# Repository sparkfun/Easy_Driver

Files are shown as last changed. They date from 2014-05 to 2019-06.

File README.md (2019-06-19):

Easy Driver
===========

Easy Driver

[*Easy Driver (ROB-12779)*](https://www.sparkfun.com/products/12779)

The EasyDriver is a simple to use stepper motor driver, compatible with anything that can output a digital 0 to 5V pulse (or 0 to 3.3V pulse if you solder SJ2 closed on the EasyDriver). 
The EasyDriver requires a 7V to 20V supply to power the motor and can power any voltage of stepper motor.

Repository Contents
-------------------
* **/Firmware** - Any firmware that the part ships with, 
* **/Hardware** - All Eagle design files (.brd, .sch, .STL)
* **/Production** - Test bed files and production panel files

Documentation
--------------

* **[Hookup Guide](https://learn.sparkfun.com/tutorials/easy-driver-hook-up-guide)** - Basic hookup guide for the Easy Driver.
* **[Brian Schmalz: Easy Driver](http://schmalzhaus.com/EasyDriver/)** - More specs and FAQ.

License Information
-------------------

_Note: This product is a collaboration with Brian Schmalz. A portion of each sales goes back to him for product support and continued development._

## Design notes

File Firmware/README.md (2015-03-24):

SparkFun Easy Driver Example Code
======================================

Repository Contents
-------------------
* **/Arduija_Demo** - Firmware for the [Arduija Project](https://www.sparkfun.com/news/1631). 
* **/SparkFun_Easy_Driver_Basic_Demo** - Firmware for the [Easy Driver Hookup Guide](https://learn.sparkfun.com/tutorials/easy-driver-hook-up-guide).
* **/EasyDriver_Example1** -Example 1 from SchmalzHaus. 
* **/EasyDriver_Example2** -Example 2 from SchmalzHaus. 
* **/EasyDriver_Example3** -Example 3 from SchmalzHaus. 
* **/EasyDriver_Example4** -Example 4 from SchmalzHaus. 
* **/EasyDriver_Example5** -Example 5 from SchmalzHaus.

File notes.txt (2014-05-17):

EasyDriver Notes.txt

A file to keep thoughts about each version, test results, changes, etc.

10/27/2013 (Just ideas/wishes at this point)
	For v4.5, add current limiting resistors to all inputs
	For v4.5, add pull downs to STEP and DIR (ALL inputs have pull down or pull ups)
	For v4.5, add P-FET reverse polarity protection
	For v4.5, make 3.3/5 switch a cuttable jumper + .1" header for easy re-setting (change SJ1 and SJ2)
	
02/25/2014
	SparkFun requested:
	For v4.5 switch to normal SparkFun 0603 footprints for all Rs and Cs (done)
	For v4.5 add date code to version number (done)
	For v4.5 add OSHW logo to board (done) 
	For v4.5 update silk screen for 10K trimpot so it's right  (done)
	For v4.5 Update 10K trimpot footprint based on part SparkFun is actually using - TRIMPOT-3MM-2 - for part 22AR10KLFTR (done)

05/16/2014 v4.5 Prototype Testing
* Minimum voltage necessary to trigger STEP and DIRECTION inputs (M+ at 12V):
	* Existing v4.5 design (R18 and R18 before the pulldowns)
		* At 5V Vcc, 2.9V is needed to trigger STEP and DIR
		* At 3.3V Vcc, 2.0V is needed to trigger STEP and DIR
	* With R18 and R19 after the pulldowns (rather than before), 
		* At 5V Vcc, 2.7V needed for STEP and DIR
		* Ad 3.3V Vcc, 1.8V needed for STEP and DIR
* Vcc measurements (M+ at 12V):
	* With 3/5V jumper open (default) : 5.027V
	* With 3/5V jumper closed : 3.300V
* TP1 needs to not have solder mask over it, and needs to be bigger in order to be easy to hit with a volt meter probe.
* Recommend SparkFun set pot so that TP1 = 2V. This will set the coil current at about 333mA
* Recommend changing R5 to 2.4K. This gives complete lower range to VRef and thus allows lower current limits for smaller stepper motors. Tested this out by replacing R5 (5.1K) with 2.4K resistor, and low end current now works much better. Minimum coil current (with Current Adjustment Pot set CW and R5=2.4K) = 145mA/phase.
* Maximum coil current measured (with Current Adjustment Pot set CCW) = 840mA/phase
* Confirmed proper operation of MS1/MS2/ENABLE/SLEEP/RESET inputs
* Tested four different NEMA-12 motors, all had good performance given various M+ input voltages, step speeds, and current pot adjustment values.
* Tested M+ input voltage from 5V to 30V. Properly adjusting step speed and current limit pot gave good performance over entire range.

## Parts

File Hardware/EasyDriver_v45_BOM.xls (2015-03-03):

EasyDriver V4.5 BOM
Qty | Ref | Description | Mfg Part Number | Disti part number | Distributor
1 | IC1 | A3967 driver chip | A3967SLBTR-T | 59P3273 | Newark
1 | C3 | CAP 47UF 35V ELECT MZA SMD | EMZA350ADA470MF61G | 565-2558-1-ND | DigiKey
1 | C1 | CAP CER .10UF 50V Y5V 0603 | C1608Y5V1H104Z | 445-1324-1-ND | DigiKey
2 | C4,C5 | CAP 680PF 50V CERAMIC X7R 0603 | CC0603KRX7R9BB681 | 311-1188-1-ND | DigiKey
2 | R3,R4 | RES 20K OHM 1/10W 5% 0603 SMD | MCR03EZPJ203 | RHM20KGCT-ND | DigiKey
2 | R1,R2 | RES .75 OHM 1/4W 1% 0805 SMD | MCR10EZHFLR750 | RHM.75MCT-ND | DigiKey
1 | IC2 | IC REG ADJ 3-TERM SOT-223-4 | LM317MDCYR | 296-12631-1-ND | DigiKey
1 | C2 | CAP 1UF 10V CER Y5V SMD 0603 | C0603C105Z8VACTU | 399-3216-1-ND | DigiKey
1 | R16 | TRIMMER 10K OHM 0.125W SMD | 22AR10KLFTR | 987-1004-1-ND | DigiKey
1 | R5 | RES 2.4K OHM 1/10W 5% 0603 SMD | RC0603JR-072K4L | 311-2.4KGRCT-ND | DigiKey
1 | PWR_LED | LED YELLOW 591NM 0603 SMD (2mA, 1.8V) | LY L29K-H1K2-26 | 475-1196-1-ND | DigiKey
8 | R10,R11,R12,R13,R14,R15,R20,R21 | RES 10K OHM 1/10W 5% 0603 SMD | ERJ-3GEYJ103V | P10KGCT-ND | DigiKey
3 | R9,R18,R19 | RES 1.0K OHM 1/10W 5% 0603 SMD | ERJ-3GEYJ102V | P1.0KGCT-ND | DigiKey
1 | R8 | RES 240 OHM 1/10W 5% 0603 SMD | ERJ-3GEYJ241V | P240GCT-ND | DigiKey
1 | R7 | RES 330 OHM 1/10W 5% 0603 SMD | ERJ-3GEYJ331V | P330GCT-ND | DigiKey
1 | R6 | RES 390 OHM 1/10W 5% 0603 SMD | ERJ-3GEYJ391V | P390GCT-ND | DigiKey
1 | R17 | RES SMD 6.8K OHM 5% 1/10W 0603 | RC0603JR-076K8L | 311-6.8KGRCT-ND | DigiKey

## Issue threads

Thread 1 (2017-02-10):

errors w/ FULL2WIRE ?

FrankOcean11, 2017-02-10:
Hello there im just inquiring about a error that im getting from a example 7 found in
http://www.schmalzhaus.com/EasyDriver/Examples/EasyDriverExamples.html

im not sure but this is the error im getting:

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

i assume it must be a BigEasy fix.

also here is the original example for further clarification:

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

EmbeddedMan, 2017-02-10:
To try and reproduce this problem, I copied and pasted Example 7 from the
web page into Arduino IDE (that has Accelstepper installed) and compiled.
It generated no warnings or errors for me. (Arduino IDE 1.8.1, compiling
for Arduino Uno)

What version of AccelStepper do you have installed? The latest version as
of right now is 1.56, and can be downloaded  here :
http://www.airspayce.com/mikem/arduino/AccelStepper/AccelStepper-1.56.zip

*Brian

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

FrankOcean11, 2017-02-10:
ok thanks that helped although now i noticed that it does not follows some of the serial calls such as "r" for reverse or 1 by it's sign, any ideas why? it will accept s & f as well as 1,2 & 3 but that r

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

EmbeddedMan, 2017-02-10:
Frank,

I'm not sure I understand your question. Are you wondering why the 'r'
command sets the 'sign' variable to -1?

*Brian

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

FrankOcean11, 2017-02-10:
no but why isn't it working?

FrankOcean11, 2017-02-10:
every command it's accepted BUT reverse

EmbeddedMan, 2017-02-10:
Hmm. I'm not sure. All of the commands should work - I know they did when I
first wrote this example. When I get home from work today I'll have to set
up this example and try out the 'r' command and see if I can duplicate the
problem.

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

FrankOcean11, 2017-02-10:
yes i start that sketch at S because i do not want it just running at start right, then ill have to open the serial window to input the command i want F, S or the non working one R as i already have it set at 3 which is 1000 but R just gets ignore, ill even hit S the R and it ill spin in the same dir as if i would have hit F instead so it looks like F&R are given out the same val of 1 and never -1 respectfully. but thanks for having a look at it.

FrankOcean11, 2017-02-10:
im not sure but i think the issue might be here

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
or it might be here or both

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

EmbeddedMan, 2017-02-11:
Frank,

I found the problem immediately when trying out the sketch. I can't believe
I had this bug in there the whole time!

Instead of FULL2WIRE, you need to change it to DRIVER. So the line should
looks like :

AccelStepper stepper(AccelStepper::DRIVER, 8, 9);

I will be updating the example web page shortly. Once you make this change,
the sketch should work as intended.

Background: Accelstepper can control all sorts of different types of
stepper drivers. Easy Driver and Big Easy Driver fall into the category of
STEP and DIRECTION drivers, which in the Accelstepper library are called
"DRIVER". So any time you use an ED or BED with Accelstepper, you must
initalize the Accelsteper object with the DRIVER parameter so it knows to
use the STEP/DIR code, rather than one of the other types. (I think it
supports up to 7 different types now.)

Give that a try and let me know if it works for you.

*Brian

*Brian

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

FrankOcean11, 2017-02-11:
No it doesent spin in reverse

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

EmbeddedMan, 2017-02-11:
Hmm. There must be something different with your setup - it spins both
directions for me. I have a motor hooked up to an Easy Driver and a
FubarinoMini (which will operate the same as an Arduino).

If you type 's' to start spinning, then '3' to go fast, then you can do 'f'
or 'r' all you want and it will go forward and reverse.

If it's not working for you, make sure that the connection from pin 3 to
the DIR input on the BED is solid, and make sure you have a good ground
connection from the BED to your Arduino.

Does it go both directions if you use Example 2?

*Brian

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

FrankOcean11, 2017-02-11:
Did you just said to type s to start? S is to stop why would it start? And
you can hit 1,2 or 3-and it won't go anywhere till you hit f or r in which
case it will only spin in the same direction, I will recheck the connection
and get back yo you, thanks for the feedback give me a few mins, btw do you
know any tips besides checking ohms values from the 4 wires?

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

EmbeddedMan, 2017-02-11:
Frank,

Yes, quite correct. S is for stop. My mistake.

Brian

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

FrankOcean11, 2017-02-12:
Well good thing i buy everything in bulk, i did pull out 2 additional sets "drivers & Steppers" and the issue is in the first Driver i was using to run test on, one of the pins on the ic must of shortened although not visible nor smells but i confirmed this by using that same stepper i been using on a new driver and all your commands worked flawlessly, thanks for your efforts and the update.

FrankOcean11, 2017-02-12:
ok i think im on to something new but im not sure maybe is just my code this time as everything im using it's new, please look at my code and tell me if you see something wrong, because i just hooked the full system connection (HW & SW) and im lacking individual control "meaning both motors are running in the same direction although i only called one" and to top it off i have to enter double digits such as aa or dd / rr or ff to get the command to register.

> note i just have 2 simple functions being called in loop in which serial is going to get one of those 2 commands respectfully to run the motors in their respected polarity using char c or e.

```
#include <AccelStepper.h>
//#include <SoftwareSerial.h>
//FULL2WIRE, DRIVER
AccelStepper Lear(AccelStepper::DRIVER, 2, 3);
AccelStepper Rear(AccelStepper::DRIVER, 4, 5);

int spd = 200;    // The current speed in steps/second
int sign = 0;      // Either 1, 0 or -1

int spd2 = 200;
int sign2 = 0;

void setup()
{
  Serial.begin(9600);
  Lear.setMaxSpeed(1000);
  Lear.setSpeed(0);
  Rear.setMaxSpeed(1000);
  Rear.setSpeed(0);
}

void loop()
{
  earA();
  earB();
}

void earA() {
  char c;
  if (Serial.available()) {
    c = Serial.read();
    if (c == 'f') {  // forward
      sign = 1;
    }
    if (c == 'r') {  // reverse
      sign = -1;
    }
    if (c == 's') {  // stop
      sign = 0;
    }
    if (c == '1') {  // super slow
      spd = 200;
    }
    if (c == '2') {  // medium
      spd = 500;
    }
    if (c == '3') {  // fast
      spd = 1000;
    }
    Lear.setSpeed(sign * spd);
  }
  Lear.runSpeed();
}

void earB() {
  char e;
  if (Serial.available()) {
    e = Serial.read();
    if (e == 'd') {  // forward
      sign = 1;
    }
    if (e == 'a') {  // reverse
      sign = -1;
    }
    if (e == 'x') {  // stop
      sign = 0;
    }
    if (e == '4') {  // super slow
      spd = 200;
    }
    if (e == '5') {  // medium
      spd = 500;
    }
    if (e == '6') {  // fast
      spd = 1000;
    }
    Rear.setSpeed(sign2 * spd2);
  }
  Rear.runSpeed();
}
```

EmbeddedMan, 2017-02-12:
Frank,

Since you've confirmed that the example sketch works properly for you, I
think we can close this particular issue.

If you need help debugging your sketch, please feel free to email me
directly, or post to the AccelStepper help list or SparkFun's forums.

This GitHub repo is really for hardware related issues with the Easy Driver
board.

*Brian

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

FrankOcean11, 2017-02-12:
no i understand but what if this is a issue where the libraries aren't working with multiple steppers? but if you insist whats your email Brian?

EmbeddedMan, 2017-02-12:
Frank,

Even so, the problem is not with the electrical design of the board itself.
This repo doesn't really have anything to do with any particular libraries
or software.

My email is on all of the Easy Driver web pages.

Brian

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

Closed 2017-02-13.

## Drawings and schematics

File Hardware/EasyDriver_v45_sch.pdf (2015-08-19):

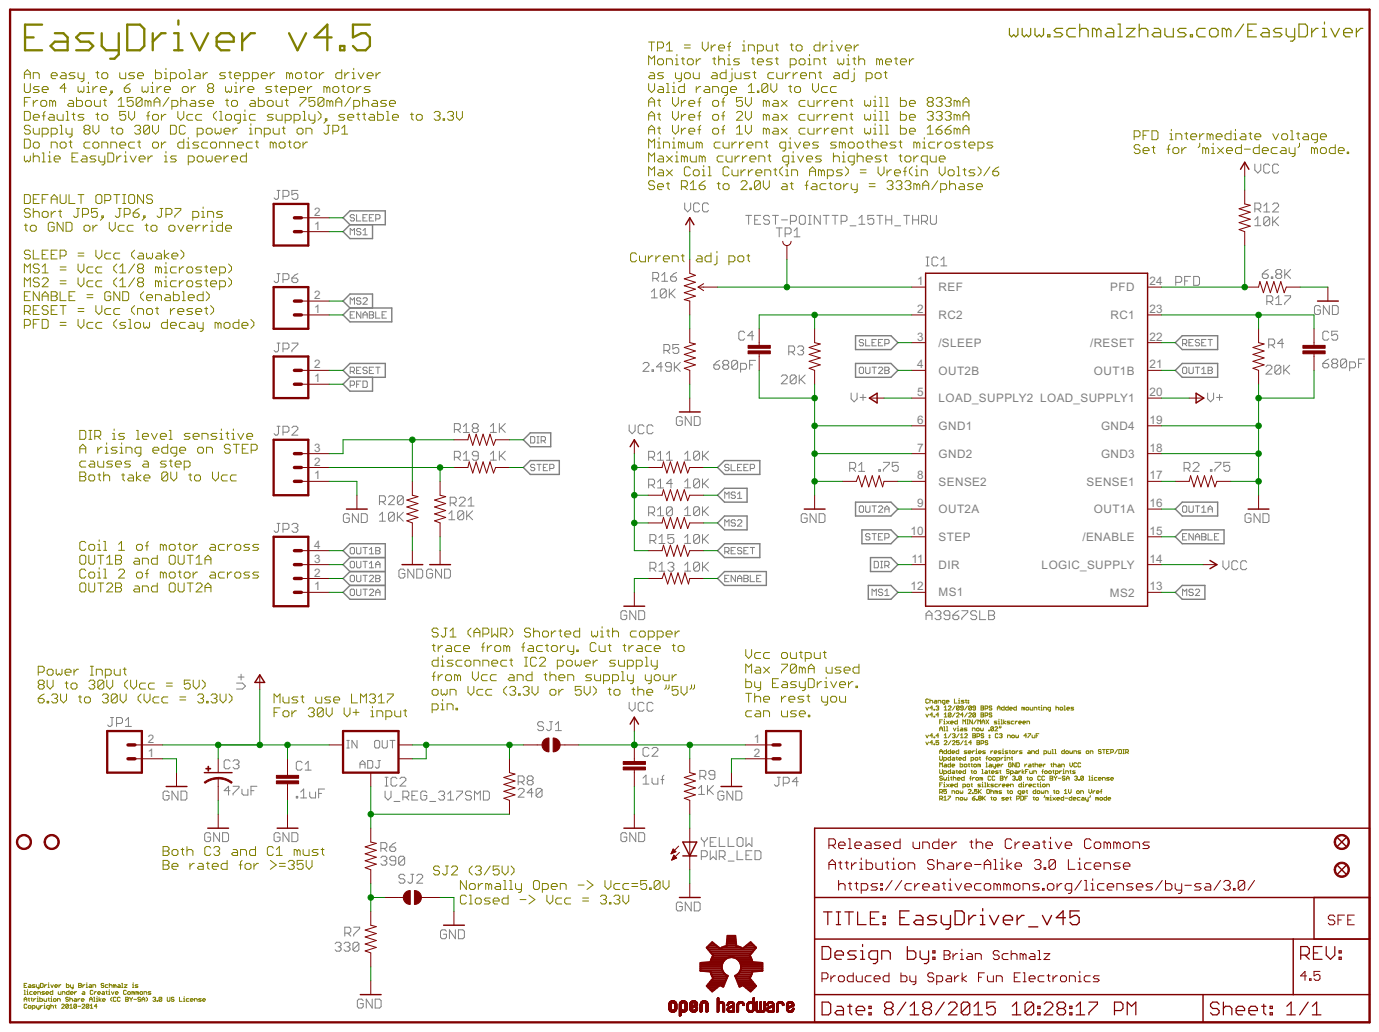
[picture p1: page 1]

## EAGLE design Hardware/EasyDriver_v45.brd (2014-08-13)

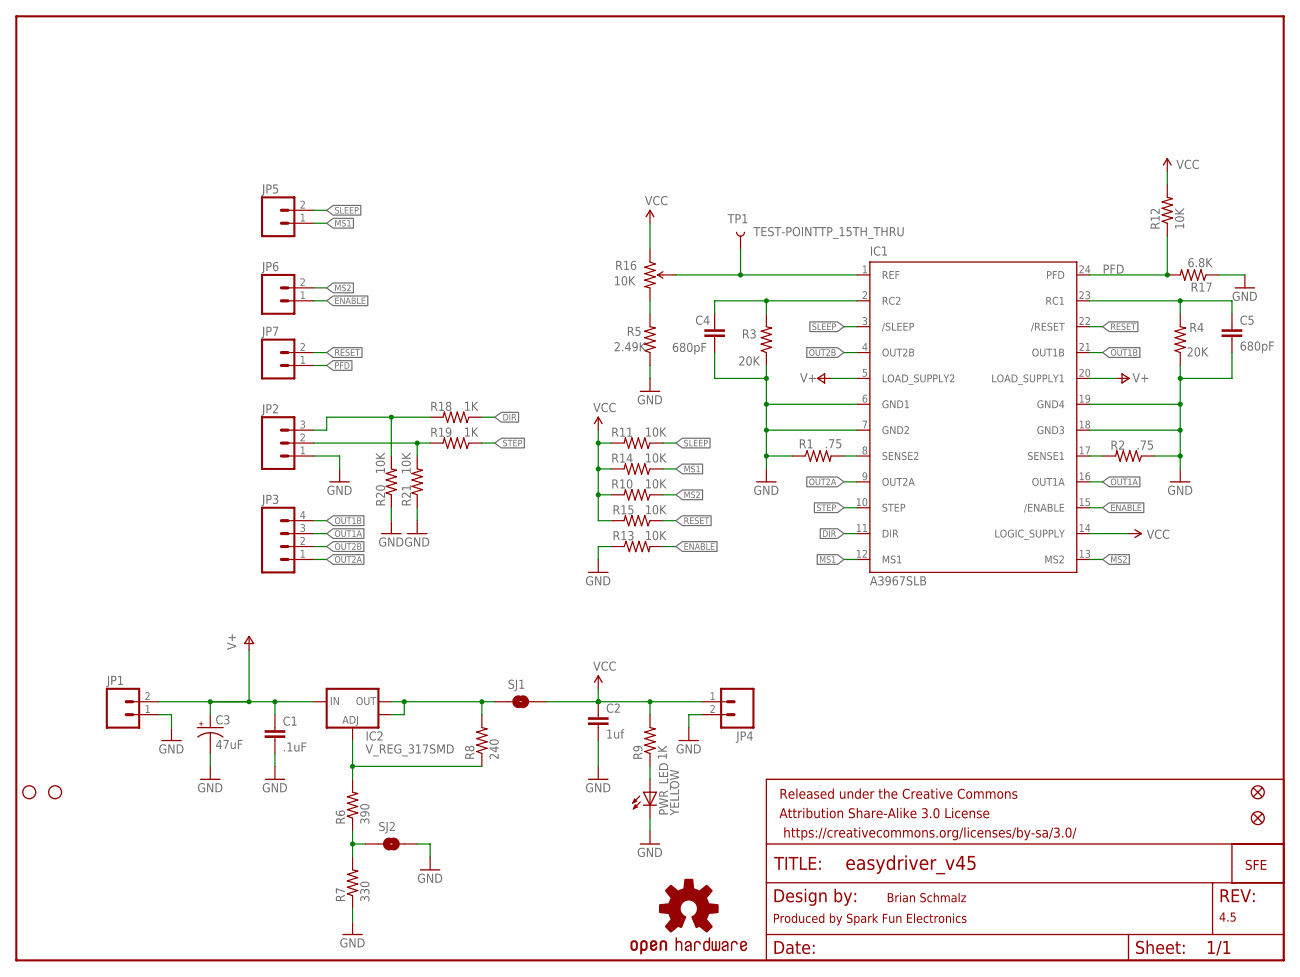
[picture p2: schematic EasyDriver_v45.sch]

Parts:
C1: .1uF; 0603-CAP
C2: 1uf; 0603-CAP
C3: 47uF; PANASONIC_D
C4, C5: 680pF; 0603-CAP
FID1, FID2: FIDUCIAL1X2; FIDUCIAL-1X2
FRAME2: FRAME-LETTER; CREATIVE_COMMONS
IC1: A3967SLB; SO24W
IC2: V_REG_317SMD; SOT223
JP1, JP4, JP5, JP6, JP7: M021X02_NO_SILK; 1X02_NO_SILK
JP2: M031X03_NO_SILK; 1X03_NO_SILK
JP3: M041X04_NO_SILK; 1X04_NO_SILK
JP8, JP9: STAND-OFF
LOGO1: OSHW-LOGOS; OSHW-LOGO-S
PWR_LED: YELLOW; LED-0603
R1, R2: .75; 0805
R3, R4: 20K; 0603-RES
R5: 2.49K; 0603-RES
R6: 390; 0603-RES
R7: 330; 0603-RES
R8: 240; 0603-RES
R9, R18, R19: 1K; 0603-RES
R10, R11, R12, R13, R14, R15, R20, R21: 10K; 0603-RES
R16: 10K; TRIMPOT-3MM-2
R17: 6.8K; 0603-RES
SJ1: SOLDERJUMPERTRACE; SJ_2S-TRACE
SJ2: SOLDERJUMPERNO; SJ_2S-NO
TP1: TEST-POINTTP_15TH_THRU; TP_15TH
U$2: LOGO-SFENEW; SFE-NEW-WEBLOGO

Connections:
5V_ALT: IC2.2 (OUT), IC2.4 (OUT), R8.2, SJ1.1
DIR: IC1.11 (DIR), R18.1
DIR_IN: JP2.3, R18.2, R20.2
ENABLE: IC1.15 (/ENABLE), JP6.1, R13.2
GND: C1.2, C2.2, C3.-, C4.2, C5.2, IC1.6 (GND1), IC1.7 (GND2), IC1.18 (GND3), IC1.19 (GND4), JP1.1, JP2.1, JP4.2, PWR_LED.C, R1.1, R2.1, R3.1, R4.1, R5.1, R7.1, R13.1, R17.1, R20.1, R21.1, SJ2.2
MS1: IC1.12 (MS1), JP5.1, R14.1
MS2: IC1.13 (MS2), JP6.2, R10.1
unnamed: IC1.8 (SENSE2), R1.2
unnamed: PWR_LED.A, R9.1
unnamed: IC1.17 (SENSE1), R2.2
unnamed: R6.1, R7.2, SJ2.1
unnamed: C4.1, IC1.2 (RC2), R3.2
unnamed: IC2.1 (ADJ), R6.2, R8.1
unnamed: C5.1, IC1.23 (RC1), R4.2
unnamed: R5.2, R16.3 (CW)
OUT1A: IC1.16 (OUT1A), JP3.3
OUT1B: IC1.21 (OUT1B), JP3.4
OUT2A: IC1.9 (OUT2A), JP3.1
OUT2B: IC1.4 (OUT2B), JP3.2
PFD: IC1.24 (PFD), JP7.1, R12.1, R17.2
RESET: IC1.22 (/RESET), JP7.2, R15.1
SLEEP: IC1.3 (/SLEEP), JP5.2, R11.1
STEP: IC1.10 (STEP), R19.1
STEP_IN: JP2.2, R19.2, R21.2
V+: C1.1, C3.+, IC1.5 (LOAD_SUPPLY2), IC1.20 (LOAD_SUPPLY1), IC2.3 (IN), JP1.2
VCC: C2.1, IC1.14 (LOGIC_SUPPLY), JP4.1, R9.2, R10.2, R11.2, R12.2, R14.2, R15.2, R16.1 (CCW), SJ1.2
VREF: IC1.1 (REF), R16.2 (WIPER), TP1.P$1

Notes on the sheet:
Brian Schmalz
Produced by Spark Fun Electronics
4.5

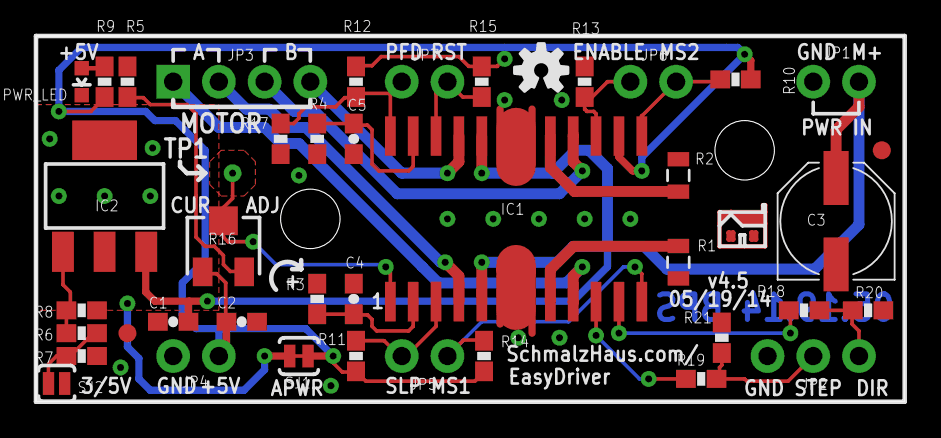
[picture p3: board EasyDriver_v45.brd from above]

Board: 2 copper layers, 48.3 x 20.3 mm, 47 parts (1 on the bottom side), 27 nets.

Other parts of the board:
U$1: SCHMALZHAUS_SMALL

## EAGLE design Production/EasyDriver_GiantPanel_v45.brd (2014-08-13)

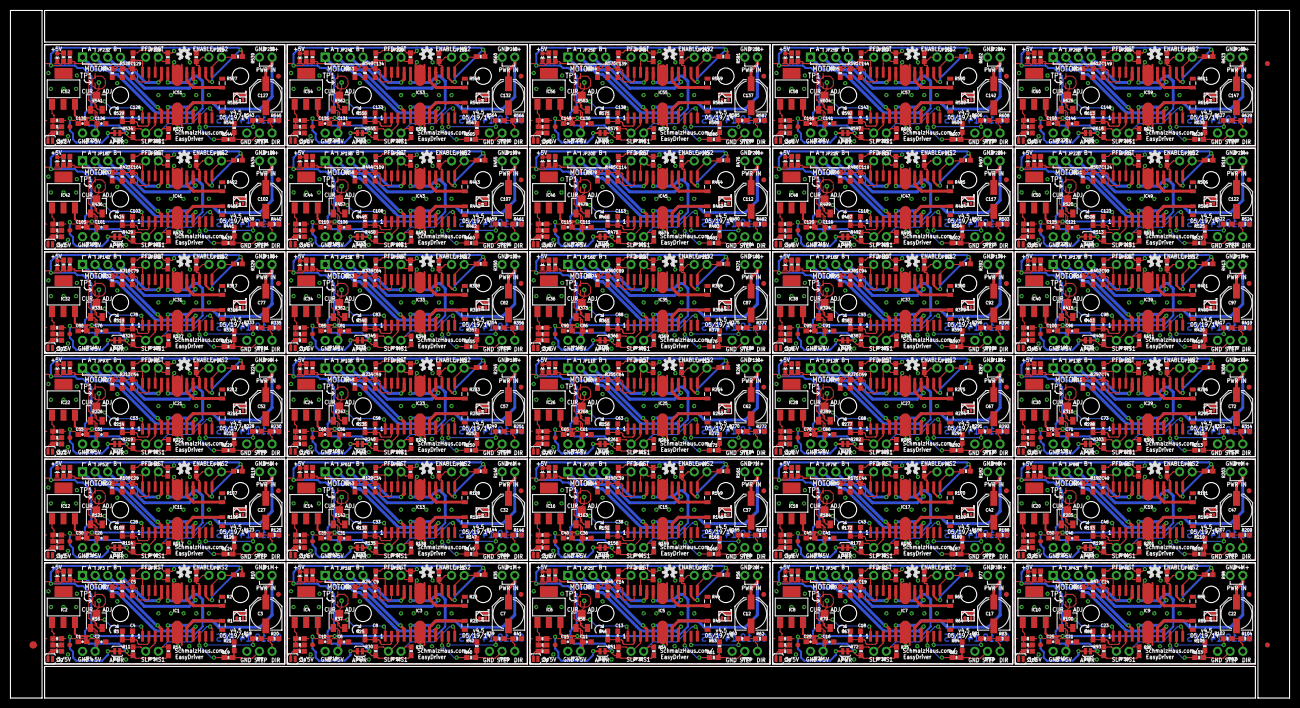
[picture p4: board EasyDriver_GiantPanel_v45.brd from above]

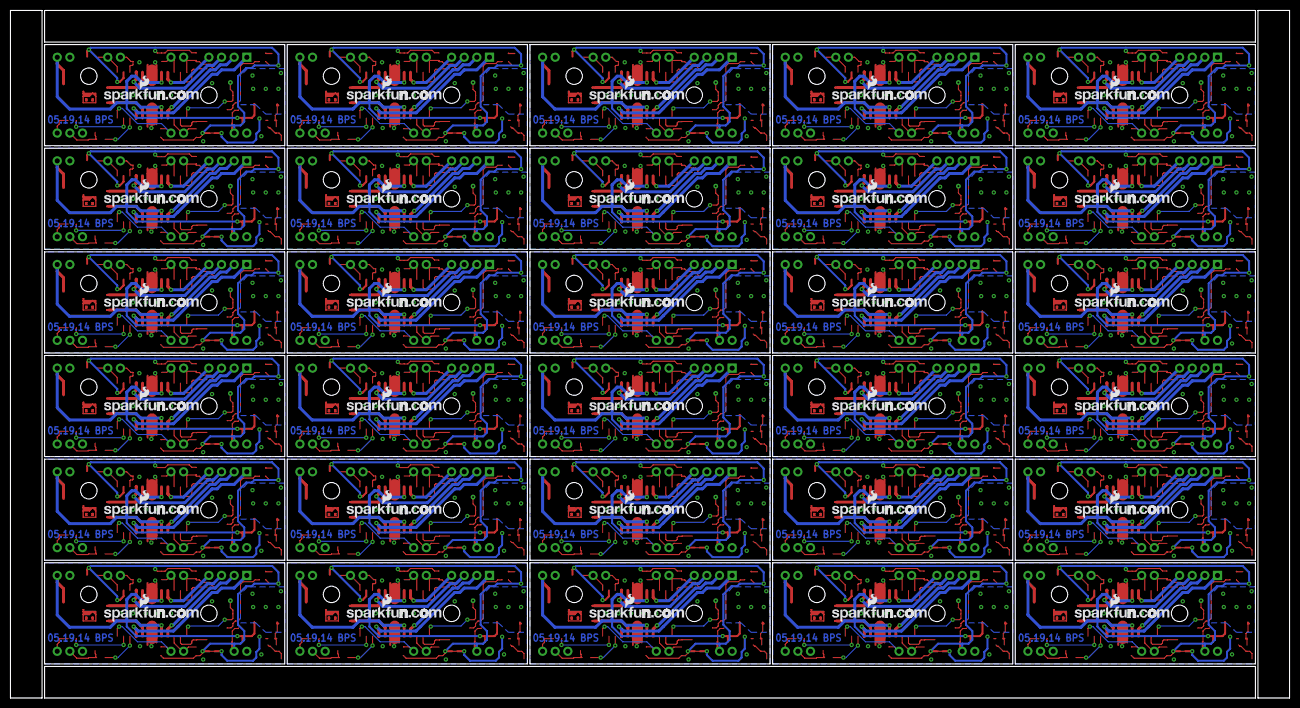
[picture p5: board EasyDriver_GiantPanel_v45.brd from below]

Board: 2 copper layers, 257.0 x 138.2 mm, 1383 parts (30 on the bottom side), 810 nets.

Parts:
C1, C10, C15, C20, C25, C30, C35, C40, C45, C50, C55, C60, C65, C70, C75, C80, C85, C90, C95, C100, C105, C110, C115, C120, C125, C130, C135, C140, C145, C150: .1uF; 0603-CAP
C2, C6, C11, C16, C21, C26, C31, C36, C41, C46, C51, C56, C61, C66, C71, C76, C81, C86, C91, C96, C101, C106, C111, C116, C121, C126, C131, C136, C141, C146: 1uf; 0603-CAP
C3, C7, C12, C17, C22, C27, C32, C37, C42, C47, C52, C57, C62, C67, C72, C77, C82, C87, C92, C97, C102, C107, C112, C117, C122, C127, C132, C137, C142, C147: 47uF; PANASONIC_D
C4, C5, C8, C9, C13, C14, C18, C19, C23, C24, C28, C29, C33, C34, C38, C39, C43, C44, C48, C49, C53, C54, C58, C59, C63, C64, C68, C69, C73, C74, C78, C79, C83, C84, C88, C89, C93, C94, C98, C99, C103, C104, C108, C109, C113, C114, C118, C119, C123, C124, C128, C129, C133, C134, C138, C139, C143, C144, C148, C149: 680pF; 0603-CAP
E$1: FIDUCIAL-1.5X3
E$4, E$6: FIDUCIAL-1X2
FID1, FID2, FID3, FID4, FID5, FID6, FID7, FID8, FID9, FID10, FID11, FID12, FID13, FID14, FID15, FID16, FID17, FID18, FID19, FID20, FID21, FID22, FID23, FID24, FID25, FID26, FID27, FID28, FID29, FID30, FID31, FID32, FID33, FID34, FID35, FID36, FID37, FID38, FID39, FID40, FID41, FID42, FID43, FID44, FID45, FID46, FID47, FID48, FID49, FID50, FID51, FID52, FID53, FID54, FID55, FID56, FID57, FID58, FID59, FID60: FIDUCIAL1X2; FIDUCIAL-1X2
IC1, IC3, IC5, IC7, IC9, IC11, IC13, IC15, IC17, IC19, IC21, IC23, IC25, IC27, IC29, IC31, IC33, IC35, IC37, IC39, IC41, IC43, IC45, IC47, IC49, IC51, IC53, IC55, IC57, IC59: A3967SLB; SO24W
IC2, IC4, IC6, IC8, IC10, IC12, IC14, IC16, IC18, IC20, IC22, IC24, IC26, IC28, IC30, IC32, IC34, IC36, IC38, IC40, IC42, IC44, IC46, IC48, IC50, IC52, IC54, IC56, IC58, IC60: V_REG_317SMD; SOT223
JP1, JP4, JP5, JP6, JP7, JP12, JP13, JP14, JP17, JP18, JP21, JP22, JP23, JP26, JP27, JP30, JP31, JP32, JP35, JP36, JP39, JP40, JP41, JP44, JP45, JP48, JP49, JP50, JP53, JP54, JP57, JP58, JP59, JP62, JP63, JP66, JP67, JP68, JP71, JP72, JP75, JP76, JP77, JP80, JP81, JP84, JP85, JP86, JP89, JP90, JP93, JP94, JP95, JP98, JP99, JP102, JP103, JP104, JP107, JP108, JP111, JP112, JP113, JP116, JP117, JP120, JP121, JP122, JP125, JP126, JP129, JP130, JP131, JP134, JP135, JP138, JP139, JP140, JP143, JP144, JP147, JP148, JP149, JP152, JP153, JP156, JP157, JP158, JP161, JP162, JP165, JP166, JP167, JP170, JP171, JP174, JP175, JP176, JP179, JP180, JP183, JP184, JP185, JP188, JP189, JP192, JP193, JP194, JP197, JP198, JP201, JP202, JP203, JP206, JP207, JP210, JP211, JP212, JP215, JP216, JP219, JP220, JP221, JP224, JP225, JP228, JP229, JP230, JP233, JP234, JP237, JP238, JP239, JP242, JP243, JP246, JP247, JP248, JP251, JP252, JP255, JP256, JP257, JP260, JP261, JP264, JP265, JP266, JP269, JP270: 1X02_NO_SILK
JP2, JP15, JP24, JP33, JP42, JP51, JP60, JP69, JP78, JP87, JP96, JP105, JP114, JP123, JP132, JP141, JP150, JP159, JP168, JP177, JP186, JP195, JP204, JP213, JP222, JP231, JP240, JP249, JP258, JP267: 1X03_NO_SILK
JP3, JP16, JP25, JP34, JP43, JP52, JP61, JP70, JP79, JP88, JP97, JP106, JP115, JP124, JP133, JP142, JP151, JP160, JP169, JP178, JP187, JP196, JP205, JP214, JP223, JP232, JP241, JP250, JP259, JP268: 1X04_NO_SILK
JP8, JP9, JP10, JP11, JP19, JP20, JP28, JP29, JP37, JP38, JP46, JP47, JP55, JP56, JP64, JP65, JP73, JP74, JP82, JP83, JP91, JP92, JP100, JP101, JP109, JP110, JP118, JP119, JP127, JP128, JP136, JP137, JP145, JP146, JP154, JP155, JP163, JP164, JP172, JP173, JP181, JP182, JP190, JP191, JP199, JP200, JP208, JP209, JP217, JP218, JP226, JP227, JP235, JP236, JP244, JP245, JP253, JP254, JP262, JP263: STAND-OFF
LOGO1, LOGO2, LOGO3, LOGO4, LOGO5, LOGO6, LOGO7, LOGO8, LOGO9, LOGO10, LOGO11, LOGO12, LOGO13, LOGO14, LOGO15, LOGO16, LOGO17, LOGO18, LOGO19, LOGO20, LOGO21, LOGO22, LOGO23, LOGO24, LOGO25, LOGO26, LOGO27, LOGO28, LOGO29, LOGO30: OSHW-LOGOS; OSHW-LOGO-S
PWR_LED, PWR_LED1, PWR_LED2, PWR_LED3, PWR_LED4, PWR_LED5, PWR_LED6, PWR_LED7, PWR_LED8, PWR_LED9, PWR_LED10, PWR_LED11, PWR_LED12, PWR_LED13, PWR_LED14, PWR_LED15, PWR_LED16, PWR_LED17, PWR_LED18, PWR_LED19, PWR_LED20, PWR_LED21, PWR_LED22, PWR_LED23, PWR_LED24, PWR_LED25, PWR_LED26, PWR_LED27, PWR_LED28, PWR_LED29: YELLOW; LED-0603
R1, R2, R22, R23, R43, R44, R64, R65, R85, R86, R106, R107, R127, R128, R148, R149, R169, R170, R190, R191, R211, R212, R232, R233, R253, R254, R274, R275, R295, R296, R316, R317, R337, R338, R358, R359, R379, R380, R400, R401, R421, R422, R442, R443, R463, R464, R484, R485, R505, R506, R526, R527, R547, R548, R568, R569, R589, R590, R610, R611: .75; 0805
R3, R4, R24, R25, R45, R46, R66, R67, R87, R88, R108, R109, R129, R130, R150, R151, R171, R172, R192, R193, R213, R214, R234, R235, R255, R256, R276, R277, R297, R298, R318, R319, R339, R340, R360, R361, R381, R382, R402, R403, R423, R424, R444, R445, R465, R466, R486, R487, R507, R508, R528, R529, R549, R550, R570, R571, R591, R592, R612, R613: 20K; 0603-RES
R5, R26, R47, R68, R89, R110, R131, R152, R173, R194, R215, R236, R257, R278, R299, R320, R341, R362, R383, R404, R425, R446, R467, R488, R509, R530, R551, R572, R593, R614: 2.49K; 0603-RES
R6, R27, R48, R69, R90, R111, R132, R153, R174, R195, R216, R237, R258, R279, R300, R321, R342, R363, R384, R405, R426, R447, R468, R489, R510, R531, R552, R573, R594, R615: 390; 0603-RES
R7, R36, R57, R78, R99, R120, R141, R162, R183, R204, R225, R246, R267, R288, R309, R330, R351, R372, R393, R414, R435, R456, R477, R498, R519, R540, R561, R582, R603, R624: 330; 0603-RES
R8, R28, R49, R70, R91, R112, R133, R154, R175, R196, R217, R238, R259, R280, R301, R322, R343, R364, R385, R406, R427, R448, R469, R490, R511, R532, R553, R574, R595, R616: 240; 0603-RES
R9, R18, R19, R29, R39, R40, R50, R60, R61, R71, R81, R82, R92, R102, R103, R113, R123, R124, R134, R144, R145, R155, R165, R166, R176, R186, R187, R197, R207, R208, R218, R228, R229, R239, R249, R250, R260, R270, R271, R281, R291, R292, R302, R312, R313, R323, R333, R334, R344, R354, R355, R365, R375, R376, R386, R396, R397, R407, R417, R418, R428, R438, R439, R449, R459, R460, R470, R480, R481, R491, R501, R502, R512, R522, R523, R533, R543, R544, R554, R564, R565, R575, R585, R586, R596, R606, R607, R617, R627, R628: 1K; 0603-RES
R10, R11, R12, R13, R14, R15, R20, R21, R30, R31, R32, R33, R34, R35, R41, R42, R51, R52, R53, R54, R55, R56, R62, R63, R72, R73, R74, R75, R76, R77, R83, R84, R93, R94, R95, R96, R97, R98, R104, R105, R114, R115, R116, R117, R118, R119, R125, R126, R135, R136, R137, R138, R139, R140, R146, R147, R156, R157, R158, R159, R160, R161, R167, R168, R177, R178, R179, R180, R181, R182, R188, R189, R198, R199, R200, R201, R202, R203, R209, R210, R219, R220, R221, R222, R223, R224, R230, R231, R240, R241, R242, R243, R244, R245, R251, R252, R261, R262, R263, R264, R265, R266, R272, R273, R282, R283, R284, R285, R286, R287, R293, R294, R303, R304, R305, R306, R307, R308, R314, R315, R324, R325, R326, R327, R328, R329, R335, R336, R345, R346, R347, R348, R349, R350, R356, R357, R366, R367, R368, R369, R370, R371, R377, R378, R387, R388, R389, R390, R391, R392, R398, R399, R408, R409, R410, R411, R412, R413, R419, R420, R429, R430, R431, R432, R433, R434, R440, R441, R450, R451, R452, R453, R454, R455, R461, R462, R471, R472, R473, R474, R475, R476, R482, R483, R492, R493, R494, R495, R496, R497, R503, R504, R513, R514, R515, R516, R517, R518, R524, R525, R534, R535, R536, R537, R538, R539, R545, R546, R555, R556, R557, R558, R559, R560, R566, R567, R576, R577, R578, R579, R580, R581, R587, R588, R597, R598, R599, R600, R601, R602, R608, R609, R618, R619, R620, R621, R622, R623, R629, R630: 10K; 0603-RES
R16, R37, R58, R79, R100, R121, R142, R163, R184, R205, R226, R247, R268, R289, R310, R331, R352, R373, R394, R415, R436, R457, R478, R499, R520, R541, R562, R583, R604, R625: 10K; TRIMPOT-3MM-2
R17, R38, R59, R80, R101, R122, R143, R164, R185, R206, R227, R248, R269, R290, R311, R332, R353, R374, R395, R416, R437, R458, R479, R500, R521, R542, R563, R584, R605, R626: 6.8K; 0603-RES
SJ1, SJ3, SJ5, SJ7, SJ9, SJ11, SJ13, SJ15, SJ17, SJ19, SJ21, SJ23, SJ25, SJ27, SJ29, SJ31, SJ33, SJ35, SJ37, SJ39, SJ41, SJ43, SJ45, SJ47, SJ49, SJ51, SJ53, SJ55, SJ57, SJ59: SOLDERJUMPERTRACE; SJ_2S-TRACE
SJ2, SJ4, SJ6, SJ8, SJ10, SJ12, SJ14, SJ16, SJ18, SJ20, SJ22, SJ24, SJ26, SJ28, SJ30, SJ32, SJ34, SJ36, SJ38, SJ40, SJ42, SJ44, SJ46, SJ48, SJ50, SJ52, SJ54, SJ56, SJ58, SJ60: SOLDERJUMPERNO; SJ_2S-NO
TP1, TP2, TP3, TP4, TP5, TP6, TP7, TP8, TP9, TP10, TP11, TP12, TP13, TP14, TP15, TP16, TP17, TP18, TP19, TP20, TP21, TP22, TP23, TP24, TP25, TP26, TP27, TP28, TP29, TP30: TEST-POINTTP_15TH_THRU; TP_15TH
U$1, U$3, U$5, U$7, U$9, U$11, U$13, U$15, U$17, U$19, U$21, U$23, U$25, U$27, U$29, U$31, U$33, U$35, U$37, U$39, U$41, U$43, U$45, U$47, U$49, U$51, U$53, U$55, U$57, U$59: SCHMALZHAUS_SMALL
U$2, U$4, U$6, U$8, U$10, U$12, U$14, U$16, U$18, U$20, U$22, U$24, U$26, U$28, U$30, U$32, U$34, U$36, U$38, U$40, U$42, U$44, U$46, U$48, U$50, U$52, U$54, U$56, U$58, U$60: LOGO-SFENEW; SFE-NEW-WEBLOGO

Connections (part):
5V_ALT: IC2.2, IC2.4, R8.2, SJ1.1
5V_ALT1: IC4.2, IC4.4, R28.2, SJ3.1
5V_ALT2: IC6.2, IC6.4, R49.2, SJ5.1
5V_ALT3: IC8.2, IC8.4, R70.2, SJ7.1
5V_ALT4: IC10.2, IC10.4, R91.2, SJ9.1
5V_ALT5: IC12.2, IC12.4, R112.2, SJ11.1
5V_ALT6: IC14.2, IC14.4, R133.2, SJ13.1
5V_ALT7: IC16.2, IC16.4, R154.2, SJ15.1
5V_ALT8: IC18.2, IC18.4, R175.2, SJ17.1
5V_ALT9: IC20.2, IC20.4, R196.2, SJ19.1
5V_ALT10: IC22.2, IC22.4, R217.2, SJ21.1
5V_ALT11: IC24.2, IC24.4, R238.2, SJ23.1
5V_ALT12: IC26.2, IC26.4, R259.2, SJ25.1
5V_ALT13: IC28.2, IC28.4, R280.2, SJ27.1
5V_ALT14: IC30.2, IC30.4, R301.2, SJ29.1
5V_ALT15: IC32.2, IC32.4, R322.2, SJ31.1
5V_ALT16: IC34.2, IC34.4, R343.2, SJ33.1
5V_ALT17: IC36.2, IC36.4, R364.2, SJ35.1
5V_ALT18: IC38.2, IC38.4, R385.2, SJ37.1
5V_ALT19: IC40.2, IC40.4, R406.2, SJ39.1
5V_ALT20: IC42.2, IC42.4, R427.2, SJ41.1
5V_ALT21: IC44.2, IC44.4, R448.2, SJ43.1
5V_ALT22: IC46.2, IC46.4, R469.2, SJ45.1
5V_ALT23: IC48.2, IC48.4, R490.2, SJ47.1
5V_ALT24: IC50.2, IC50.4, R511.2, SJ49.1
5V_ALT25: IC52.2, IC52.4, R532.2, SJ51.1
5V_ALT26: IC54.2, IC54.4, R553.2, SJ53.1
5V_ALT27: IC56.2, IC56.4, R574.2, SJ55.1
5V_ALT28: IC58.2, IC58.4, R595.2, SJ57.1
5V_ALT29: IC60.2, IC60.4, R616.2, SJ59.1
DIR: IC1.11, R18.1
DIR1: IC3.11, R39.1
DIR2: IC5.11, R60.1
DIR3: IC7.11, R81.1
DIR4: IC9.11, R102.1
DIR5: IC11.11, R123.1
DIR6: IC13.11, R144.1
DIR7: IC15.11, R165.1
DIR8: IC17.11, R186.1
DIR9: IC19.11, R207.1
DIR10: IC21.11, R228.1
DIR11: IC23.11, R249.1
DIR12: IC25.11, R270.1
DIR13: IC27.11, R291.1
DIR14: IC29.11, R312.1
DIR15: IC31.11, R333.1
DIR16: IC33.11, R354.1
DIR17: IC35.11, R375.1
DIR18: IC37.11, R396.1
DIR19: IC39.11, R417.1
DIR20: IC41.11, R438.1
DIR21: IC43.11, R459.1
DIR22: IC45.11, R480.1
DIR23: IC47.11, R501.1
DIR24: IC49.11, R522.1
DIR25: IC51.11, R543.1
DIR26: IC53.11, R564.1
DIR27: IC55.11, R585.1
DIR28: IC57.11, R606.1
DIR29: IC59.11, R627.1
DIR_IN: JP2.3, R18.2, R20.2
DIR_IN1: JP15.3, R39.2, R41.2
DIR_IN2: JP24.3, R60.2, R62.2
DIR_IN3: JP33.3, R81.2, R83.2
DIR_IN4: JP42.3, R102.2, R104.2
DIR_IN5: JP51.3, R123.2, R125.2
DIR_IN6: JP60.3, R144.2, R146.2
DIR_IN7: JP69.3, R165.2, R167.2
DIR_IN8: JP78.3, R186.2, R188.2
DIR_IN9: JP87.3, R207.2, R209.2
DIR_IN10: JP96.3, R228.2, R230.2
DIR_IN11: JP105.3, R249.2, R251.2
DIR_IN12: JP114.3, R270.2, R272.2
DIR_IN13: JP123.3, R291.2, R293.2
DIR_IN14: JP132.3, R312.2, R314.2
DIR_IN15: JP141.3, R333.2, R335.2
DIR_IN16: JP150.3, R354.2, R356.2
DIR_IN17: JP159.3, R375.2, R377.2
DIR_IN18: JP168.3, R396.2, R398.2
DIR_IN19: JP177.3, R417.2, R419.2
DIR_IN20: JP186.3, R438.2, R440.2
DIR_IN21: JP195.3, R459.2, R461.2
DIR_IN22: JP204.3, R480.2, R482.2
DIR_IN23: JP213.3, R501.2, R503.2
DIR_IN24: JP222.3, R522.2, R524.2
DIR_IN25: JP231.3, R543.2, R545.2
DIR_IN26: JP240.3, R564.2, R566.2
DIR_IN27: JP249.3, R585.2, R587.2
DIR_IN28: JP258.3, R606.2, R608.2
DIR_IN29: JP267.3, R627.2, R629.2
ENABLE: IC1.15, JP6.1, R13.2
ENABLE1: IC3.15, JP13.1, R32.2
ENABLE2: IC5.15, JP22.1, R53.2
ENABLE3: IC7.15, JP31.1, R74.2
ENABLE4: IC9.15, JP40.1, R95.2
ENABLE5: IC11.15, JP49.1, R116.2
ENABLE6: IC13.15, JP58.1, R137.2
ENABLE7: IC15.15, JP67.1, R158.2
ENABLE8: IC17.15, JP76.1, R179.2
ENABLE9: IC19.15, JP85.1, R200.2
ENABLE10: IC21.15, JP94.1, R221.2
ENABLE11: IC23.15, JP103.1, R242.2
ENABLE12: IC25.15, JP112.1, R263.2
ENABLE13: IC27.15, JP121.1, R284.2
ENABLE14: IC29.15, JP130.1, R305.2
ENABLE15: IC31.15, JP139.1, R326.2
ENABLE16: IC33.15, JP148.1, R347.2
ENABLE17: IC35.15, JP157.1, R368.2
ENABLE18: IC37.15, JP166.1, R389.2
ENABLE19: IC39.15, JP175.1, R410.2
ENABLE20: IC41.15, JP184.1, R431.2
ENABLE21: IC43.15, JP193.1, R452.2
ENABLE22: IC45.15, JP202.1, R473.2
ENABLE23: IC47.15, JP211.1, R494.2
ENABLE24: IC49.15, JP220.1, R515.2
ENABLE25: IC51.15, JP229.1, R536.2
ENABLE26: IC53.15, JP238.1, R557.2
ENABLE27: IC55.15, JP247.1, R578.2
ENABLE28: IC57.15, JP256.1, R599.2
ENABLE29: IC59.15, JP265.1, R620.2
GND: C1.2, C2.2, C3.-, C4.2, C5.2, IC1.6, IC1.7, IC1.18, IC1.19, JP1.1, JP2.1, JP4.2, PWR_LED.C, R1.1, R2.1, R3.1, R4.1, R5.1, R7.1, R13.1, R17.1, R20.1, R21.1, SJ2.2
GND1: C6.2, C7.-, C8.2, C9.2, C10.2, IC3.6, IC3.7, IC3.18, IC3.19, JP15.1, JP17.1, JP18.2, PWR_LED1.C, R22.1, R23.1, R24.1, R25.1, R26.1, R32.1, R36.1, R38.1, R41.1, R42.1, SJ4.2
GND2: C11.2, C12.-, C13.2, C14.2, C15.2, IC5.6, IC5.7, IC5.18, IC5.19, JP24.1, JP26.1, JP27.2, PWR_LED2.C, R43.1, R44.1, R45.1, R46.1, R47.1, R53.1, R57.1, R59.1, R62.1, R63.1, SJ6.2
GND3: C16.2, C17.-, C18.2, C19.2, C20.2, IC7.6, IC7.7, IC7.18, IC7.19, JP33.1, JP35.1, JP36.2, PWR_LED3.C, R64.1, R65.1, R66.1, R67.1, R68.1, R74.1, R78.1, R80.1, R83.1, R84.1, SJ8.2
GND4: C21.2, C22.-, C23.2, C24.2, C25.2, IC9.6, IC9.7, IC9.18, IC9.19, JP42.1, JP44.1, JP45.2, PWR_LED4.C, R85.1, R86.1, R87.1, R88.1, R89.1, R95.1, R99.1, R101.1, R104.1, R105.1, SJ10.2
GND5: C26.2, C27.-, C28.2, C29.2, C30.2, IC11.6, IC11.7, IC11.18, IC11.19, JP51.1, JP53.1, JP54.2, PWR_LED5.C, R106.1, R107.1, R108.1, R109.1, R110.1, R116.1, R120.1, R122.1, R125.1, R126.1, SJ12.2
GND6: C31.2, C32.-, C33.2, C34.2, C35.2, IC13.6, IC13.7, IC13.18, IC13.19, JP60.1, JP62.1, JP63.2, PWR_LED6.C, R127.1, R128.1, R129.1, R130.1, R131.1, R137.1, R141.1, R143.1, R146.1, R147.1, SJ14.2
GND7: C36.2, C37.-, C38.2, C39.2, C40.2, IC15.6, IC15.7, IC15.18, IC15.19, JP69.1, JP71.1, JP72.2, PWR_LED7.C, R148.1, R149.1, R150.1, R151.1, R152.1, R158.1, R162.1, R164.1, R167.1, R168.1, SJ16.2
GND8: C41.2, C42.-, C43.2, C44.2, C45.2, IC17.6, IC17.7, IC17.18, IC17.19, JP78.1, JP80.1, JP81.2, PWR_LED8.C, R169.1, R170.1, R171.1, R172.1, R173.1, R179.1, R183.1, R185.1, R188.1, R189.1, SJ18.2
GND9: C46.2, C47.-, C48.2, C49.2, C50.2, IC19.6, IC19.7, IC19.18, IC19.19, JP87.1, JP89.1, JP90.2, PWR_LED9.C, R190.1, R191.1, R192.1, R193.1, R194.1, R200.1, R204.1, R206.1, R209.1, R210.1, SJ20.2
GND10: C51.2, C52.-, C53.2, C54.2, C55.2, IC21.6, IC21.7, IC21.18, IC21.19, JP96.1, JP98.1, JP99.2, PWR_LED10.C, R211.1, R212.1, R213.1, R214.1, R215.1, R221.1, R225.1, R227.1, R230.1, R231.1, SJ22.2
GND11: C56.2, C57.-, C58.2, C59.2, C60.2, IC23.6, IC23.7, IC23.18, IC23.19, JP105.1, JP107.1, JP108.2, PWR_LED11.C, R232.1, R233.1, R234.1, R235.1, R236.1, R242.1, R246.1, R248.1, R251.1, R252.1, SJ24.2
GND12: C61.2, C62.-, C63.2, C64.2, C65.2, IC25.6, IC25.7, IC25.18, IC25.19, JP114.1, JP116.1, JP117.2, PWR_LED12.C, R253.1, R254.1, R255.1, R256.1, R257.1, R263.1, R267.1, R269.1, R272.1, R273.1, SJ26.2
GND13: C66.2, C67.-, C68.2, C69.2, C70.2, IC27.6, IC27.7, IC27.18, IC27.19, JP123.1, JP125.1, JP126.2, PWR_LED13.C, R274.1, R275.1, R276.1, R277.1, R278.1, R284.1, R288.1, R290.1, R293.1, R294.1, SJ28.2
GND14: C71.2, C72.-, C73.2, C74.2, C75.2, IC29.6, IC29.7, IC29.18, IC29.19, JP132.1, JP134.1, JP135.2, PWR_LED14.C, R295.1, R296.1, R297.1, R298.1, R299.1, R305.1, R309.1, R311.1, R314.1, R315.1, SJ30.2
GND15: C76.2, C77.-, C78.2, C79.2, C80.2, IC31.6, IC31.7, IC31.18, IC31.19, JP141.1, JP143.1, JP144.2, PWR_LED15.C, R316.1, R317.1, R318.1, R319.1, R320.1, R326.1, R330.1, R332.1, R335.1, R336.1, SJ32.2
GND16: C81.2, C82.-, C83.2, C84.2, C85.2, IC33.6, IC33.7, IC33.18, IC33.19, JP150.1, JP152.1, JP153.2, PWR_LED16.C, R337.1, R338.1, R339.1, R340.1, R341.1, R347.1, R351.1, R353.1, R356.1, R357.1, SJ34.2
GND17: C86.2, C87.-, C88.2, C89.2, C90.2, IC35.6, IC35.7, IC35.18, IC35.19, JP159.1, JP161.1, JP162.2, PWR_LED17.C, R358.1, R359.1, R360.1, R361.1, R362.1, R368.1, R372.1, R374.1, R377.1, R378.1, SJ36.2
GND18: C91.2, C92.-, C93.2, C94.2, C95.2, IC37.6, IC37.7, IC37.18, IC37.19, JP168.1, JP170.1, JP171.2, PWR_LED18.C, R379.1, R380.1, R381.1, R382.1, R383.1, R389.1, R393.1, R395.1, R398.1, R399.1, SJ38.2
GND19: C96.2, C97.-, C98.2, C99.2, C100.2, IC39.6, IC39.7, IC39.18, IC39.19, JP177.1, JP179.1, JP180.2, PWR_LED19.C, R400.1, R401.1, R402.1, R403.1, R404.1, R410.1, R414.1, R416.1, R419.1, R420.1, SJ40.2
GND20: C101.2, C102.-, C103.2, C104.2, C105.2, IC41.6, IC41.7, IC41.18, IC41.19, JP186.1, JP188.1, JP189.2, PWR_LED20.C, R421.1, R422.1, R423.1, R424.1, R425.1, R431.1, R435.1, R437.1, R440.1, R441.1, SJ42.2
GND21: C106.2, C107.-, C108.2, C109.2, C110.2, IC43.6, IC43.7, IC43.18, IC43.19, JP195.1, JP197.1, JP198.2, PWR_LED21.C, R442.1, R443.1, R444.1, R445.1, R446.1, R452.1, R456.1, R458.1, R461.1, R462.1, SJ44.2
GND22: C111.2, C112.-, C113.2, C114.2, C115.2, IC45.6, IC45.7, IC45.18, IC45.19, JP204.1, JP206.1, JP207.2, PWR_LED22.C, R463.1, R464.1, R465.1, R466.1, R467.1, R473.1, R477.1, R479.1, R482.1, R483.1, SJ46.2
GND23: C116.2, C117.-, C118.2, C119.2, C120.2, IC47.6, IC47.7, IC47.18, IC47.19, JP213.1, JP215.1, JP216.2, PWR_LED23.C, R484.1, R485.1, R486.1, R487.1, R488.1, R494.1, R498.1, R500.1, R503.1, R504.1, SJ48.2
GND24: C121.2, C122.-, C123.2, C124.2, C125.2, IC49.6, IC49.7, IC49.18, IC49.19, JP222.1, JP224.1, JP225.2, PWR_LED24.C, R505.1, R506.1, R507.1, R508.1, R509.1, R515.1, R519.1, R521.1, R524.1, R525.1, SJ50.2
GND25: C126.2, C127.-, C128.2, C129.2, C130.2, IC51.6, IC51.7, IC51.18, IC51.19, JP231.1, JP233.1, JP234.2, PWR_LED25.C, R526.1, R527.1, R528.1, R529.1, R530.1, R536.1, R540.1, R542.1, R545.1, R546.1, SJ52.2
GND26: C131.2, C132.-, C133.2, C134.2, C135.2, IC53.6, IC53.7, IC53.18, IC53.19, JP240.1, JP242.1, JP243.2, PWR_LED26.C, R547.1, R548.1, R549.1, R550.1, R551.1, R557.1, R561.1, R563.1, R566.1, R567.1, SJ54.2
GND27: C136.2, C137.-, C138.2, C139.2, C140.2, IC55.6, IC55.7, IC55.18, IC55.19, JP249.1, JP251.1, JP252.2, PWR_LED27.C, R568.1, R569.1, R570.1, R571.1, R572.1, R578.1, R582.1, R584.1, R587.1, R588.1, SJ56.2
GND28: C141.2, C142.-, C143.2, C144.2, C145.2, IC57.6, IC57.7, IC57.18, IC57.19, JP258.1, JP260.1, JP261.2, PWR_LED28.C, R589.1, R590.1, R591.1, R592.1, R593.1, R599.1, R603.1, R605.1, R608.1, R609.1, SJ58.2
GND29: C146.2, C147.-, C148.2, C149.2, C150.2, IC59.6, IC59.7, IC59.18, IC59.19, JP267.1, JP269.1, JP270.2, PWR_LED29.C, R610.1, R611.1, R612.1, R613.1, R614.1, R620.1, R624.1, R626.1, R629.1, R630.1, SJ60.2
MS1: IC1.12, JP5.1, R14.1
MS2: IC1.13, JP6.2, R10.1
MS3: IC3.12, JP12.1, R33.1
MS4: IC3.13, JP13.2, R35.1
MS5: IC5.12, JP21.1, R54.1
MS6: IC5.13, JP22.2, R56.1
MS7: IC7.12, JP30.1, R75.1
MS8: IC7.13, JP31.2, R77.1
MS9: IC9.12, JP39.1, R96.1
MS10: IC9.13, JP40.2, R98.1
MS11: IC11.12, JP48.1, R117.1
MS12: IC11.13, JP49.2, R119.1
MS13: IC13.12, JP57.1, R138.1
MS14: IC13.13, JP58.2, R140.1
MS15: IC15.12, JP66.1, R159.1
MS16: IC15.13, JP67.2, R161.1
MS17: IC17.12, JP75.1, R180.1
MS18: IC17.13, JP76.2, R182.1
MS19: IC19.12, JP84.1, R201.1
MS20: IC19.13, JP85.2, R203.1
MS21: IC21.12, JP93.1, R222.1
MS22: IC21.13, JP94.2, R224.1
MS23: IC23.12, JP102.1, R243.1
MS24: IC23.13, JP103.2, R245.1
MS25: IC25.12, JP111.1, R264.1
MS26: IC25.13, JP112.2, R266.1
MS27: IC27.12, JP120.1, R285.1
MS28: IC27.13, JP121.2, R287.1
MS29: IC29.12, JP129.1, R306.1
MS30: IC29.13, JP130.2, R308.1
MS31: IC31.12, JP138.1, R327.1
MS32: IC31.13, JP139.2, R329.1
MS33: IC33.12, JP147.1, R348.1
MS34: IC33.13, JP148.2, R350.1
MS35: IC35.12, JP156.1, R369.1
MS36: IC35.13, JP157.2, R371.1
MS37: IC37.12, JP165.1, R390.1
MS38: IC37.13, JP166.2, R392.1
MS39: IC39.12, JP174.1, R411.1
MS40: IC39.13, JP175.2, R413.1
MS41: IC41.12, JP183.1, R432.1
MS42: IC41.13, JP184.2, R434.1
MS43: IC43.12, JP192.1, R453.1
MS44: IC43.13, JP193.2, R455.1
MS45: IC45.12, JP201.1, R474.1
MS46: IC45.13, JP202.2, R476.1
MS47: IC47.12, JP210.1, R495.1
MS48: IC47.13, JP211.2, R497.1
MS49: IC49.12, JP219.1, R516.1
MS50: IC49.13, JP220.2, R518.1
MS51: IC51.12, JP228.1, R537.1
MS52: IC51.13, JP229.2, R539.1
MS53: IC53.12, JP237.1, R558.1
MS54: IC53.13, JP238.2, R560.1
MS55: IC55.12, JP246.1, R579.1
MS56: IC55.13, JP247.2, R581.1
MS57: IC57.12, JP255.1, R600.1
MS58: IC57.13, JP256.2, R602.1
MS59: IC59.12, JP264.1, R621.1
MS60: IC59.13, JP265.2, R623.1
unnamed: IC1.8, R1.2
unnamed: PWR_LED.A, R9.1
unnamed: IC1.17, R2.2
unnamed: R6.1, R7.2, SJ2.1
unnamed: C4.1, IC1.2, R3.2
unnamed: IC2.1, R6.2, R8.1
unnamed: C5.1, IC1.23, R4.2
unnamed: IC3.8, R22.2
unnamed: C8.1, IC3.2, R25.2
unnamed: C9.1, IC3.23, R24.2
unnamed: R5.2, R16.3
unnamed: IC3.17, R23.2
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

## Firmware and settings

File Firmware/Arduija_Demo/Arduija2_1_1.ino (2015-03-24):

/***********************************************************
Arduija: Arduino Controlled Ouija Board
Joel Bartlett
Casey Kuhns
SparkFun Electronics
Oct. 22, 2014
https://github.com/JoelEB/Arduija2_1_1

This sketch uses the AccelStepper Library to controll two stpper motors, 
driven by two Big Easy Driver boards from SparkFun. Letters on a Ouija 
board are mapped out, given coordinates, and then massages are spelled 
out by looking up the coordinates in that table. 

Development environment specifics:
Arduino IDE .0+
Arduino Uno

This code is beerware; if you see me at the local pub, 
and you've found our code helpful, please buy us a round!

Distributed as-is; no warranty is given. 
***********************************************************/
#include <avr/pgmspace.h>
#include <AccelStepper.h>//include the Accel Stepper Library 
#define MAX_ARRAY_LENGTH 32

// Define two steppers and the pins they will use
AccelStepper stepperX(1, 4, 5);//X axis
AccelStepper stepperY(1, 6, 7);//Y axis
//(driver=true, step, dir)

int enableX = 10;//pins to controll the enable pins on each of the Big Easy Drivers
int enableY = 11;//I tried using the intenral setEnablePin() function in the AccelStepper library
//but couldn't get it to work, even when I inverted them with setPinsInverted().

int posX = 0;//Varibales to keep track of the planchet's current position 
int posY = 0;

int switch_x_left = 8;//Limit switch variables
int switct_y_top = 9;
int switch_x_right = 3;//trying to set these up as interrupts (W.I.P.)
int switch_y_bottom = 2;

int bigButton = 12;//Added big dome pushbutotn to have it display a message when pressed.
//Original plan was to have it run constantly, but the smaller stepper motor (ROB-09238)
//gets hot when ran for even a shoirt while. I'm pushing it past it's max ratings. I would 
//recommend using a 68oz.-in. motor (ROB-10846) on both axes. Make sure you disable all motors 
//when not in use to minimize heat dissipation and power consumption. 

long randomNumber;//Random number for displaying random message when butotn is pressed.

//table to store coordinates for all the letters, #s, etc on the board. 
//Due to the nature of the magnets and drag, getting exact coordinates took 
//lots of trial an error, and is still not perfect when you have the planchet 
//move in from different sides of the letter. 
unsigned int coordinatesTable[39][3] = {
  1000,2600,'a',
  2800,1900,'b',
  4400,1700,'c',
  6100,1500,'d',
  8200,1300,'e',
  9300,1100,'f',
  11800,1200,'g',
  13700,1200,'h',
  15500,1100,'i',
  16800,1500,'j',
  18700,1700,'k',
  20300,2100,'l',
  22800,2500,'m',
  1200,4500,'n',
  2500,3900,'o',
  4300,3400,'p',
  6000,3200,'q',
  7900,2800,'r',
  9700,2600,'s',
  11500,2600,'t',
  13600,2700,'u',
  15400,2700,'v',
  17200,2800,'w',
  19400,3400,'x',
  20800,4000,'y',
  22800,4500,'z',
  0,0,'0',
  0,0,'1',
  0,0,'2',
  0,0,'3',
  0,0,'4',
  0,0,'5',
  0,0,'6',
  0,0,'8',
  0,0,'9',
  4400,10,'+',//YES
  19900,10,'-',//NO
  0,0,'!',//GOODBYE
  11700,100,'.'//SPACE
};
//------------------------------------------------------------------------------
void setup()
{  
  Serial.begin(115200);//Serial print for debug
  
  pinMode(bigButton, INPUT_PULLUP);//Pullup button so external resistor is not needed
  randomSeed(analogRead(0));//Read analog(0) for random number generation 
  
  pinMode(enableX, OUTPUT);//
  pinMode(enableY, OUTPUT);
  
  digitalWrite(enableX, HIGH);//Diable the motors 
  digitalWrite(enableY, HIGH);
  
  //Had to play with these vallues to find a speed and acceleration that looked good 
  //but also still ran smoothly. Tweeking these values and physically changing the 
  //potentiometers on the Big Easy Driver will affect the speed of each axis. 
  //BEWARE, changing these settings will change coordinates and mess up any characters 
  //you have mapped out already. 
  stepperX.setMaxSpeed(6000);
  stepperX.setAcceleration(5000);
  stepperY.setMaxSpeed(4000);
  stepperY.setAcceleration(4000);
  
  //This is the internal AccelStepper enable calls referred to 
  //earlier. Must be called within setup() (W.I.P.)
  //stepperX.setEnablePin(10);
  //stepperY.setEnablePin(11);
  //stepperX.setPinsInverted(0,0,1);//invert the enable pin
  //stepperY.setPinsInverted(0,0,1);
  
  pinMode(switch_x_left, INPUT_PULLUP);
  pinMode(switct_y_top, INPUT_PULLUP);
  pinMode(switch_x_right, INPUT_PULLUP);
  pinMode(switch_y_bottom, INPUT_PULLUP);
  //Switch interrupts to ensure the planchet never goes out of bounds (W.I.P.)
  //attachInterrupt(0, homeing2, FALLING); //switct_y_bottom
  //attachInterrupt(1, homeing2, FALLING);//switch_x_right
  
  homeing();//set the cursor back to its home position at 0,0 first and on every reset

}
//------------------------------------------------------------------------------
void loop()
{
  if(digitalRead(bigButton) == LOW)//Wait until the big dome pusbutton is pressed to start spelling a message
  {
    ouijaMessage();//Select a random message from the list and print it
  }

  //Uncomment this line and comment out everything else in loop() to jog the planchet with keyboard inputs 
  //moveWithKeyboard();
}
//------------------------------------------------------------------------------
void enableMotors()
{
  //Enable the motors 
  digitalWrite(enableX, LOW);
  digitalWrite(enableY, LOW);
}
//------------------------------------------------------------------------------
void disableMotors()
{
  //Disable the motors 
  digitalWrite(enableX, HIGH);
  digitalWrite(enableY, HIGH);
}
//------------------------------------------------------------------------------
void homeing()
{
  enableMotors();
  //Decided to move Y axis first since one of the magnets was hitting if it was all the way away from home. 
  if(digitalRead(switct_y_top) == HIGH)
  {
    while(digitalRead(switct_y_top) == HIGH)
    {
      stepperY.moveTo(posY);
      stepperY.run();
      posY = posY - 1;
      //Serial.println(posY);
    }
    if(digitalRead(switct_y_top) == LOW)
      stepperY.stop();
      posY = 0;
      stepperY.setCurrentPosition(0);
    }
  else
  {
  posY = 0;
  stepperY.setCurrentPosition(0);
  }
  
  if(digitalRead(switch_x_left) == HIGH)//check to make sure this axis isn;t already in the home posotion 
  {
    while(digitalRead(switch_x_left) == HIGH)//if it is not at home (HIGH) ...
    {
      stepperX.moveTo(posX);//start moving the X axis back to the home position
      stepperX.run();
      posX = posX - 1;//decrement the position until we reach 0 (where the switch is triggered) 
    }
    if(digitalRead(switch_x_left) == LOW)//Once the switch is hit and the signal goes LOW...
      stepperX.stop();//stop the motor
      posX = 0;//set this axis position to 0
      stepperX.setCurrentPosition(0);
  }
  else
  {
  posX = 0;
  stepperX.setCurrentPosition(0);
  }
  disableMotors();
}
//------------------------------------------------------------------------------
void ouijaDelay(void){
  //Delay to make it spoooooooky
  //Standard Delay until we can make it more spooky
   delay(200); 
}
//------------------------------------------------------------------------------
//Look through the table until a character matching the current one is found
int findSymbolInTable(char symbol){
  int tableIndex;
  
  for(tableIndex = 0; tableIndex <= 39; tableIndex++){
    //Serial.println(char((coordinatesTable[tableIndex][2])));
    if(symbol == char(coordinatesTable[tableIndex][2])){
      //Serial.print("Char FOUND = ");
      //Serial.println(tableIndex);
      return tableIndex; //Return the table location
    }
  }
     return -1; //if we got to the point
                // we didn't find our value in the table 
}

//------------------------------------------------------------------------------
//Used to move the planchet to the next location on the baord. 
void moveToSymbol(char character)
{
  int tableIndex = findSymbolInTable(character);

  //Serial.print("x = ");
  //Serial.println(coordinatesTable[tableIndex][0]);

  //Serial.print("y = ");
  //Serial.println(coordinatesTable[tableIndex][1]);
  
  //MoveMotors
  stepperX.moveTo(coordinatesTable[tableIndex][0]);
  stepperY.moveTo(coordinatesTable[tableIndex][1]);
  
  while((stepperX.distanceToGo() != 0)||(stepperX.distanceToGo() != 0)){
    //Serial.println(stepperX.distanceToGo());
    stepperY.run();
    stepperX.run();
    //if(digitalRead(switch_x_right) == LOW || digitalRead(switch_y_bottom) == LOW)
      //homeing();
  }

  return;
}


//------------------------------------------------------------------------------
void ouijaPrint(char* charArray){
  int i;
  for(i = 0; i <= MAX_ARRAY_LENGTH; i++){
    //Serial.print(charArray[i]); //Debug the array as we move
    if(charArray[i] != 0){
      ouijaDelay();
      moveToSymbol(charArray[i]);
      ouijaDelay();  
      //if(digitalRead(switch_x_right) == LOW || digitalRead(switch_y_bottom) == LOW)
      //homeing();
    } //Only move if there if valid data, if not let the loop run out.
    else break;
  }
  return;
}
//------------------------------------------------------------------------------
//Stores different messages to be speled out by the Ouija 
void ouijaMessage()
{
    enableMotors();
    randomNumber = random(5);//Generate a random number between 1-5
    switch (randomNumber) //switch messages based on that random number
    {
      case 0:
        {char arrayThing[30] = {'h','e','l','.','l','o',0};
        ouijaPrint(arrayThing);
        homeing();}//Go back to home after each massage is printed
        break;
      case 1:
        {
        char arrayThing2[30] = {'s','p','a','r','k','f','u','n',0};
        ouijaPrint(arrayThing2);
        homeing();}
        break;
      case 2:
        {
        char arrayThing3[30] = {'h','a','p','.','p','y','.','h','a','l','.','l','o','w','e','.','e','n',0};;
        ouijaPrint(arrayThing3);
      homeing();}
        break;
      case 3:
        {
        char arrayThing4[30] = {'g','r','a','n','d','m','a','.','s','a','y','s','.','h','i',0};;
        ouijaPrint(arrayThing4);
        homeing();}
        break;
      case 4:
        {
        char arrayThing5[30] = {'l','e','t','.','y','o','u','r','.','g','e','e','k','.','s','h','i','n','e',0};;
        ouijaPrint(arrayThing5);
      homeing();}
        break;
      default: 
        disableMotors();
     }
    disableMotors();
}
//------------------------------------------------------------------------------
//This function was used to jog each axis 100 "steps" in each direction 
//call in loop and comment out everything else to allow keyboard control
void moveWithKeyboard()
{
  enableMotors();
  if(Serial.available() > 0)
  {
    int temp = Serial.read();
    
    if(temp == 119 || temp == 87)//dec for 'w'
    {
      stepperY.moveTo(stepperY.currentPosition() - 100);
      //stepperY.setSpeed(2000);
      while(stepperY.distanceToGo() != 0)
      {
        stepperY.run();
      }
      Serial.print(stepperX.currentPosition());
      Serial.print("   ");
      Serial.println(stepperY.currentPosition());
    }
    if(temp == 115 || temp == 83)//dec for 's'
    {
      stepperY.moveTo(stepperY.currentPosition() + 100);
      //stepperY.setSpeed(2000);
      while(stepperY.distanceToGo() != 0)
      {
        stepperY.run();
      } 
      Serial.print(stepperX.currentPosition());
      Serial.print("   ");
      Serial.println(stepperY.currentPosition());
    }
    if(temp == 97 || temp == 65)//dec for 'a'
    {
      stepperX.moveTo(stepperX.currentPosition() - 100);
      //stepperX.setSpeed(3000);
      while(stepperX.distanceToGo() != 0)
      {
        stepperX.run();
      }  
      Serial.print(stepperX.currentPosition());
      Serial.print("   ");
      Serial.println(stepperY.currentPosition());
    }
    if(temp == 100 || temp == 68)//dec for 'd'
    {
      stepperX.moveTo(stepperX.currentPosition() + 100.00);
      //stepperX.setSpeed(3000);
      while(stepperX.distanceToGo() != 0)
      {
        stepperX.run();
      }
      Serial.print(stepperX.currentPosition());
      Serial.print("   ");
      Serial.println(stepperY.currentPosition());
    }
    
    //move in larger increments with the right side of the keyboard
    if(temp == 105 || temp == 73)//dec for 'i'
    {
      stepperY.moveTo(stepperY.currentPosition() - 1000);
      while(stepperY.distanceToGo() != 0)
      {
        stepperY.run();
      }
      Serial.print(stepperX.currentPosition()); Serial.print("   "); Serial.println(stepperY.currentPosition());
    }
    if(temp == 107 || temp == 75)//dec for 'k'
    {
      stepperY.moveTo(stepperY.currentPosition() + 1000);
      //stepperY.setSpeed(2000);
      while(stepperY.distanceToGo() != 0)
      {
        stepperY.run();
      } 
      Serial.print(stepperX.currentPosition()); Serial.print("   "); Serial.println(stepperY.currentPosition());
    }
    if(temp == 106 || temp == 74)//dec for 'j'
    {
      stepperX.moveTo(stepperX.currentPosition() - 2000);
      //stepperX.setSpeed(3000);
      while(stepperX.distanceToGo() != 0)
      {
        stepperX.run();
      }  
      Serial.print(stepperX.currentPosition()); Serial.print("   "); Serial.println(stepperY.currentPosition());
    }
    if(temp == 108 || temp == 76)//dec for 'l'
    {
      stepperX.moveTo(stepperX.currentPosition() + 2000);
      while(stepperX.distanceToGo() != 0)
      {
        stepperX.run();
      }
      Serial.print(stepperX.currentPosition()); Serial.print("   "); Serial.println(stepperY.currentPosition());
    }
  
  }
  disableMotors();
}
//------------------------------------------------------------------------------
void drawCircleCW()//(W.I.P.)
{
  enableMotors();
  stepperX.moveTo(12000);
  stepperY.moveTo(1000);
  while((stepperX.distanceToGo() != 0)||(stepperX.distanceToGo() != 0))
  {
    stepperX.run();
    stepperY.run();
  }
  
  stepperX.moveTo(14000);
  stepperY.moveTo(2000);
  while((stepperX.distanceToGo() != 0)||(stepperX.distanceToGo() != 0))
  {
    stepperX.run();
    stepperY.run();
  }
  
  stepperX.moveTo(12000);
  stepperY.moveTo(3000);
  while((stepperX.distanceToGo() != 0)||(stepperX.distanceToGo() != 0))
  {
    stepperX.run();
    stepperY.run();
  }
  
  stepperX.moveTo(8000);
  stepperY.moveTo(2000);
  while((stepperX.distanceToGo() != 0)||(stepperX.distanceToGo() != 0))
  {
    stepperX.run();
    stepperY.run();
  }
  
  stepperX.moveTo(12000);
  stepperY.moveTo(2000);
  while((stepperX.distanceToGo() != 0)||(stepperX.distanceToGo() != 0))
  {
    stepperX.run();
    stepperY.run();
  }
  disableMotors();
}

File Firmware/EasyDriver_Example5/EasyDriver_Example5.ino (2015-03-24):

// Example5 code for Brian Schmalz's Easy Driver Example page
// http://www.schmalzhaus.com/EasyDriver/EasyDriverExamples.html

#include <AccelStepper.h>

// Define the stepper and the pins it will use
AccelStepper stepper1(1, 9, 8);

// Define our three input button pins
#define  LEFT_PIN  4
#define  STOP_PIN  3
#define  RIGHT_PIN 2

// Define our analog pot input pin
#define  SPEED_PIN 0

// Define our maximum and minimum speed in steps per second (scale pot to these)
#define  MAX_SPEED 500
#define  MIN_SPEED 0.1

void setup() {
  // The only AccelStepper value we have to set here is the max speeed, which is higher than we'll ever go 
  stepper1.setMaxSpeed(10000.0);
  
  // Set up the three button inputs, with pullups
  pinMode(LEFT_PIN, INPUT_PULLUP);
  pinMode(STOP_PIN, INPUT_PULLUP);
  pinMode(RIGHT_PIN, INPUT_PULLUP);
}

void loop() {
  static float current_speed = 0.0;         // Holds current motor speed in steps/second
  static int analog_read_counter = 1000;    // Counts down to 0 to fire analog read
  static char sign = 0;                     // Holds -1, 1 or 0 to turn the motor on/off and control direction
  static int analog_value = 0;              // Holds raw analog value.
  
  // If a switch is pushed down (low), set the sign value appropriately
  if (digitalRead(LEFT_PIN) == 0) {
    sign = 1;
  }
  else if (digitalRead(RIGHT_PIN) == 0) {    
    sign = -1;
  }
  else if (digitalRead(STOP_PIN) == 0) {
    sign = 0;
  }

  // We only want to read the pot every so often (because it takes a long time we don't
  // want to do it every time through the main loop).  
  if (analog_read_counter > 0) {
    analog_read_counter--;
  }
  else {
    analog_read_counter = 3000;
    // Now read the pot (from 0 to 1023)
    analog_value = analogRead(SPEED_PIN);
    // Give the stepper a chance to step if it needs to
    stepper1.runSpeed();
    //  And scale the pot's value from min to max speeds
    current_speed = sign * ((analog_value/1023.0) * (MAX_SPEED - MIN_SPEED)) + MIN_SPEED;
    // Update the stepper to run at this new speed
    stepper1.setSpeed(current_speed);
  }

  // This will run the stepper at a constant speed
  stepper1.runSpeed();
}

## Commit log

2014-03-19 Bringing design in from SchmalzHaus SVN to SparkFun GitHub. Also new version - 4.5 - with minor updates (footprints mainly, but also some extra protection resistors.)
    [EasyDriver_v45.brd, EasyDriver_v45.dxf, EasyDriver_v45.sch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]
2014-03-28 Version 4.5 updates -
    * All Rs and Cs are now normal 0603 SparkFun footprints
    * Added series Rs and pull downs for STEP and DIR inputs
    * Updated pot footprint to TRIMPOT-3MM-2 for better soldering
    * Switched license from CC BY 3.0 to CC BY-SA 3.0
    * Fixed pot direction silk screen
    [EasyDriver_v45.brd, EasyDriver_v45.sch]
2014-04-01 Small updates to schematic and board
    * Rotated ground symbol on schematic so it matched other ground symbols
    * Changed TP1 to standard SparkFun test point footprint
    [EasyDriver_v45.brd, EasyDriver_v45.sch]
2014-05-17 Completed testing on first v4.5 prototypes, and wrote up results in notes.txt. Also added some text to schematic including formula for calculating Max Current from Vref voltage.
    [EasyDriver_v45.sch]
2014-05-20 * Made TP1 bigger, and no longer covered with solder mask * Switched R5 to 2.4K Ohms to allow Vref down to 1V into driver * Set R17 to 6.8K to allow PFD input to select 'mixed-decay' mode * Swapped l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
    [EasyDriver_v45.brd, EasyDriver_v45.sch, EasyDriver_v45_BOM.xls]
2014-05-22 Based on SparkFun feedback * Replaced frame with newest version from SparkFun library * Replaced VCC symbol with newest version from SparkFun library * Move components so that keepout area around mou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
    [EasyDriver_v45.brd, EasyDriver_v45.sch]
2014-05-23 Updating 2.4k to 2.49K resistor and updating to CC-SA 3.0
    [EasyDriver_v45.brd, EasyDriver_v45.dxf, EasyDriver_v45.sch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]
2014-08-13 added regular fiducials
    [EasyDriver_v45.brd, EasyDriver_v45.sch]
2014-08-13 created giant panel v45
    [EasyDriver_GiantPanel_v45.brd]
2015-03-03 Added BOM, updated for version 4.5
    [EasyDriver_v45_BOM.xls]
2015-03-03 Fixed 3 mistakes in the BOM: * R17 should be included in the build * R16 had wrong part number * R5 was wrong value.
    [EasyDriver_v45_BOM.xls]
2015-03-24 Adding in demo sketches, fixing directory name
    [EasyDriver_GiantPanel_v45.brd]
2015-08-19 Minor edits to some of schematic guide text for clarity of function (SJ1 mainly). Created schematic PDF so we can link to it in GitHub.
    [EasyDriver_v45.sch]

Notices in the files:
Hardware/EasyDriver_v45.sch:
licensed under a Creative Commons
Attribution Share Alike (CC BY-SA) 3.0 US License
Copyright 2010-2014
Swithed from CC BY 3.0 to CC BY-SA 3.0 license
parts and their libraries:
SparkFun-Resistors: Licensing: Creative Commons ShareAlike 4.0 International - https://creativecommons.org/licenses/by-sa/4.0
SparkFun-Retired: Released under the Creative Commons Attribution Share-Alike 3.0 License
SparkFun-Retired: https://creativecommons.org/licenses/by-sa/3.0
